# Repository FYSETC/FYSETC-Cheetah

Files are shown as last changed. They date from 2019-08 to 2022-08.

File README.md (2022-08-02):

## 1. Product Introduction

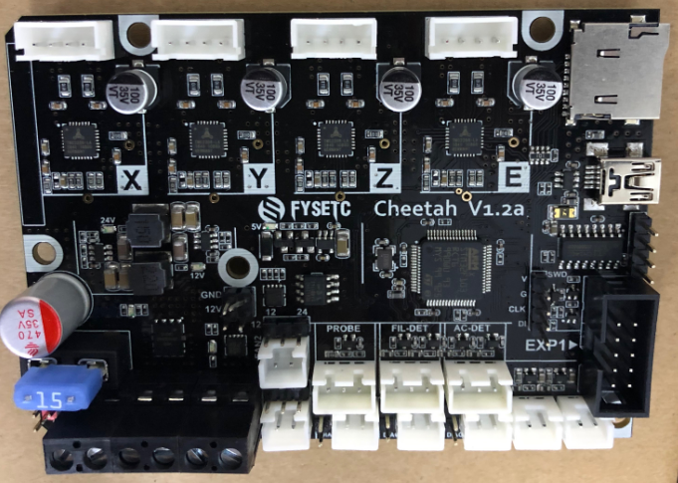
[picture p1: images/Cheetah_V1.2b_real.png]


Designed for a single-head 3D printer, many interfaces are reserved for more features. Such as AC detection, filament detection, leveling with BL-touch or other sensors.

## 2. Features

- Compact size: 101.5mm x 72mm，Compatible with the Creatlity ender 3 motherboard size

- fully integrated all in one solution:
  
  - STM32F103 MCU (Run Marlin 2.0 )
  - CH340 for high speed USB serial connection 
  - (V1.1)4X TMC2209 stepper drivers, Support sensor-less homing
  - (V1.2)4X TMC2208 stepper drivers, not support sensor-less homing

- UNIVERSAL POWER:
  
  - can be used with 7V-35V for motors / heated bed
  - (V1.2)24V to 12V/2A DC-DC for fans
  - integrated high precision power regulators (DC/DC):  5V 1A Max and 3.3V  600mA Max LDO

- Onboard TF card socket

- EXP1 for 12864 display panel (Creality 12864 panel or FYSETC Generic12864)

- Onboard RGB control (V1.2 have no RGB control)

- RGB control and fan control 12V/24V optional (Requires 24V to 12V module)

- PCB：
  
  - High quality, High temperature FR4-TG130 PCB
  - Gold ENIG finishing

## 3. Application

Check `examples` folder for more information.

- 3D printer 
- CNC Device
- Other similar machines

## 4. Hardware

### 4.1 Hardware Reasources

| Board Name | Cheetah |
| --- | --- |
| License | GPL V2.0 |
| Latest Version | V1.0 |
| Extruders | 1 |
| Fixed Fans | 2 Max |
| Controlled Fans | 1 Max |
| Heaters | 1 Max |
| Endstops | 3 Max |
| Temp sens | 2 Max |
| I2C | 1 |
| SWD | 1 |
| Serial port chip | CH340 |
| CPU | STM32F103 |
| CPU Speed ( MHz ) | 72 Mhz |
| Stepper driver | 4X TMC2209 (V1.2 = 2208) |
| Stepper driver  Type | Onboard |
| Input | 12v/24v |
| Output | BED OUT：10A Max ；Heater Out：5A Max |

### 4.2 Connectors and jumpers define(V1.1)

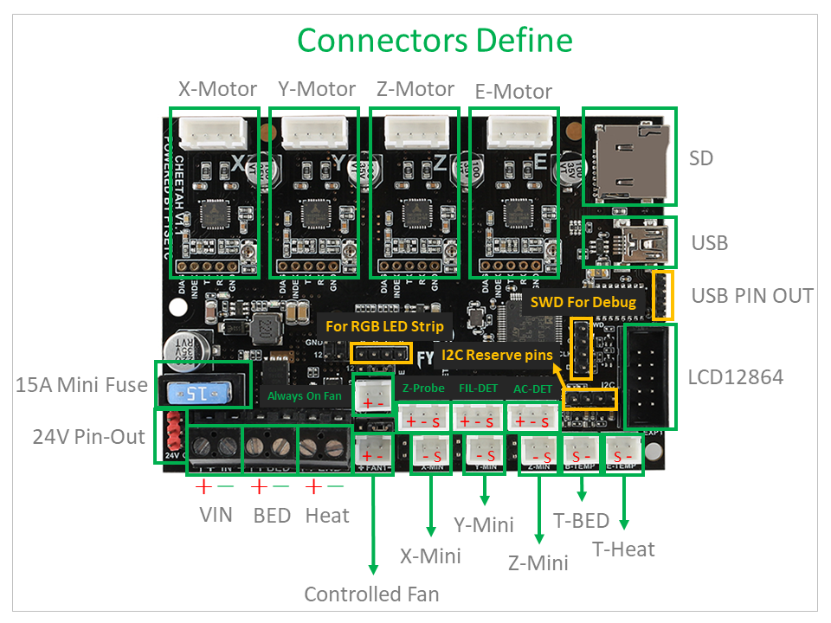
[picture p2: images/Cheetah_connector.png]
Cheetah_connectors

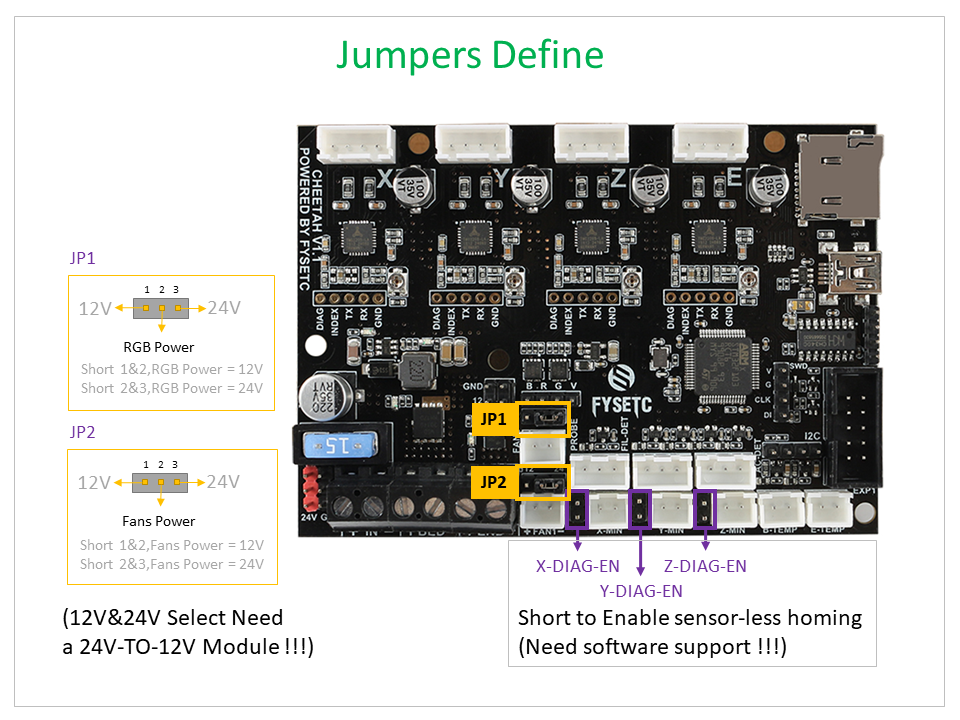
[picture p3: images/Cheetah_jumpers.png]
Cheetah_jumpers


### 4.3 Connectors and jumpers define(V1.2)

Not available.

### 4.4 Pin Definition

#### 4.4.1 Cheetah V1.1

<table>
   <tr><td>Features</td><td>Cheetah Pin</td><td>STM32 Pin</td><td>Pin No.</td><td>Comment</td></tr>
   <tr><td rowspan="3">X-MOTOR(1)</td><td>X-Step</td><td>PB8</td><td>61</td><td></td></tr>
   <tr><td>X-DIR</td><td>PB9</td><td>62</td><td></td></tr>
   <tr><td>X-EN</td><td>PA8</td><td>41</td><td></td></tr>
   <tr><td rowspan="3">Y-MOTOR(2)</td><td>Y-Step</td><td>PB2</td><td>28</td><td></td></tr>
   <tr><td>Y-DIR</td><td>PB3</td><td>55</td><td></td></tr>
   <tr><td>Y-EN</td><td>PB1</td><td>27</td><td></td></tr>
   <tr><td rowspan="3">Z-MOTOR(3)</td><td>Z-Step</td><td>PC0</td><td>8</td><td></td></tr>
   <tr><td>Z-DIR</td><td>PC1</td><td>9</td><td></td></tr>
   <tr><td>Z-EN</td><td>PC2</td><td>10</td><td></td></tr>
   <tr><td rowspan="3">E0-MOTOR(4)</td><td>E0-Step</td><td>PC15</td><td>4</td><td></td></tr>
   <tr><td>E0-DIR</td><td>PC14</td><td>3</td><td></td></tr>
   <tr><td>E0-EN</td><td>PC13</td><td>2</td><td></td></tr>
   <tr><td rowspan="2">TMC2209 SERIAL (UART2)</td><td>TX2</td><td>PA2</td><td>16</td><td></td></tr>
   <tr><td>RX2</td><td>PA3</td><td>17</td><td></td></tr>
   <tr><td rowspan="3">End-stops</td><td>X-MIN</td><td>PA1</td><td>15</td><td></td></tr>
   <tr><td>Y-MIN</td><td>PB4</td><td>56</td><td></td></tr>
   <tr><td>Z-MIN</td><td>PA15</td><td>50</td><td></td></tr>
   <tr><td rowspan="1">FAN</td><td>FAN0</td><td>PC8</td><td>39</td><td></td></tr>
   <tr><td rowspan="3">RGB</td><td>LED-R</td><td>PB0</td><td>26</td><td>Can be used for fan1</td></tr>
   <tr><td>LED-G</td><td>PB7</td><td>59</td><td>Can be used for fan2</td></tr>
   <tr><td>LED-B</td><td>PB6</td><td>58</td><td>Can be used for fan3</td></tr>
   <tr><td rowspan="2">Heating</td><td>E0-Heater</td><td>PC6</td><td>37</td><td></td></tr>
   <tr><td>Heated-Bed</td><td>PC7</td><td>38</td><td></td></tr>
   <tr><td rowspan="2">Temperature</td><td>TE0</td><td>PC4</td><td>15</td><td></td></tr>
   <tr><td>TB</td><td>PC5</td><td>18</td><td></td></tr>
   <tr><td rowspan="8">EXP1</td><td>BEEP</td><td>PC9</td><td>40</td><td></td></tr>
   <tr><td>BTN_ENC</td><td>PC12</td><td>53</td><td></td></tr>
   <tr><td>BTN_EN2</td><td>PC11</td><td>52</td><td></td></tr>
   <tr><td>MISO</td><td>PA6/MISO2</td><td>22</td><td></td></tr>
   <tr><td>BTN_EN1</td><td>PC10</td><td>51</td><td></td></tr>
   <tr><td>SCK</td><td>PA5/SCK2</td><td>21</td><td></td></tr>
   <tr><td>CS</td><td>PA4</td><td>20</td><td></td></tr>
   <tr><td>MOSI</td><td>PA7/MOSI2</td><td>23</td><td></td></tr>
   <tr><td rowspan="2">UART</td><td>TX</td><td>PA9/TX1</td><td>42</td><td></td></tr>
   <tr><td>RX</td><td>PA10/RX1</td><td>43</td><td></td></tr>
   <tr><td rowspan="2">I2C</td><td>I2C2 SCL</td><td>PB10</td><td>29</td><td></td></tr>
   <tr><td>I2C2 SDA</td><td>PB11</td><td>30</td><td></td></tr>
   <tr><td rowspan="3">SWD Debug</td><td>SWDIO</td><td>PA13</td><td>72</td><td>only used for debugging now and can be used for other purposes.</td></tr>
   <tr><td>SWCLK</td><td>PA14</td><td>76</td><td>only used for debugging now and can be used for other purposes.</td></tr>
</table>

#### 4.4.2 Cheetah V1.2

<table>
   <tr><td>Features</td><td>Cheetah Pin</td><td>STM32 Pin</td><td>Pin No.</td><td>Comment</td></tr>
   <tr><td rowspan="3">X-MOTOR(1)</td><td>X-Step</td><td>PB8</td><td>61</td><td></td></tr>
   <tr><td>X-DIR</td><td>PB9</td><td>62</td><td></td></tr>
   <tr><td>X-EN</td><td>PA8</td><td>41</td><td></td></tr>
   <tr><td rowspan="3">Y-MOTOR(2)</td><td>Y-Step</td><td>PB2</td><td>28</td><td></td></tr>
   <tr><td>Y-DIR</td><td>PB3</td><td>55</td><td></td></tr>
   <tr><td>Y-EN</td><td>PB1</td><td>27</td><td></td></tr>
   <tr><td rowspan="3">Z-MOTOR(3)</td><td>Z-Step</td><td>PC0</td><td>8</td><td></td></tr>
   <tr><td>Z-DIR</td><td>PC1</td><td>9</td><td></td></tr>
   <tr><td>Z-EN</td><td>PC2</td><td>10</td><td></td></tr>
   <tr><td rowspan="3">E0-MOTOR(4)</td><td>E0-Step</td><td>PC15</td><td>4</td><td></td></tr>
   <tr><td>E0-DIR</td><td>PC14</td><td>3</td><td></td></tr>
   <tr><td>E0-EN</td><td>PC13</td><td>2</td><td></td></tr>
   <tr><td rowspan="8">TMC2208 SERIAL</td><td>X TX</td><td>PA11</td><td>44</td><td></td></tr>
   <tr><td>X RX</td><td>PA12</td><td>45</td><td></td></tr>
   <tr><td>Y TX</td><td>PB6</td><td>58</td><td></td></tr>
   <tr><td>Y RX</td><td>PB7</td><td>59</td><td></td></tr>
   <tr><td>Z TX</td><td>PB10</td><td>29</td><td></td></tr>
   <tr><td>Z RX</td><td>PB11</td><td>30</td><td></td></tr>
   <tr><td>E TX</td><td>PA2</td><td>16</td><td></td></tr>
   <tr><td>E RX</td><td>PA3</td><td>17</td><td></td></tr>
   <tr><td rowspan="3">End-stops</td><td>X-MIN</td><td>PA1</td><td>15</td><td></td></tr>
   <tr><td>Y-MIN</td><td>PB4</td><td>56</td><td></td></tr>
   <tr><td>Z-MIN</td><td>PA15</td><td>50</td><td></td></tr>
   <tr><td rowspan="2">FAN</td><td>FAN0</td><td>PC8</td><td>39</td><td></td></tr>
   <tr><td>FAN1</td><td>PB0</td><td>26</td><td></td></tr>
   <tr><td rowspan="2">Heating</td><td>E0-Heater</td><td>PC6</td><td>37</td><td></td></tr>
   <tr><td>Heated-Bed</td><td>PC7</td><td>38</td><td></td></tr>
   <tr><td rowspan="2">Temperature</td><td>TE0</td><td>PC4</td><td>15</td><td></td></tr>
   <tr><td>TB</td><td>PC5</td><td>18</td><td></td></tr>
   <tr><td rowspan="8">EXP1</td><td>BEEP</td><td>PC9</td><td>40</td><td></td></tr>
   <tr><td>BTN_ENC</td><td>PC12</td><td>53</td><td></td></tr>
   <tr><td>BTN_EN2</td><td>PC11</td><td>52</td><td></td></tr>
   <tr><td>MISO</td><td>PA6/MISO2</td><td>22</td><td></td></tr>
   <tr><td>BTN_EN1</td><td>PC10</td><td>51</td><td></td></tr>
   <tr><td>SCK</td><td>PA5/SCK2</td><td>21</td><td></td></tr>
   <tr><td>CS</td><td>PA4</td><td>20</td><td></td></tr>
   <tr><td>MOSI</td><td>PA7/MOSI2</td><td>23</td><td></td></tr>
   <tr><td rowspan="2">UART</td><td>TX</td><td>PA9/TX1</td><td>42</td><td></td></tr>
   <tr><td>RX</td><td>PA10/RX1</td><td>43</td><td></td></tr>
   <tr><td rowspan="3">SWD Debug</td><td>SWDIO</td><td>PA13</td><td>72</td><td>only used for debugging now and can be used for other purposes.</td></tr>
   <tr><td>SWCLK</td><td>PA14</td><td>76</td><td>only used for debugging now and can be used for other purposes.</td></tr>
</table>

## 5. Firmware

### 5.1 Marlin

The FYSETC CHEETAH firmware is pre-config for ENDER3 machine, if you want to change the firmware or compile the code yourself , follow the steps.

#### 5.1.1 Download Vscode + platformio

To compile the firmware , you need to install Visual Studio Code and the platformio pulg-in.

#### 5.1.2 Firmware code

You have two code source choices :

##### Source 1

You can get Marlin code is in the `firmware/Marlin` folder in this repository [github](https://github.com/FYSETC/FYSETC-Cheetah/tree/master/firmware/Marlin) or [gitee](https://gitee.com/fysetc/FYSETC-Cheetah/tree/master/firmware/Marlin). 

And change `MOTHERBOARD` define according to your cheetah board version in `Configuration.h`

Cheetah v1.1x

```
#define MOTHERBOARD BOARD_FYSETC_CHEETAH
```

Cheetah v1.2x

```
#define MOTHERBOARD BOARD_FYSETC_CHEETAH_V12
```

##### Source 2

Also you can get upstream branch from [github](https://github.com/MarlinFirmware/Marlin) or [gitee](https://gitee.com/fysetc/Marlin). But remember to change `default_envs` in `platformio.ini` file.

```
default_envs = STM32F103RC_fysetc
```

And change `MOTHERBOARD` define according to your cheetah board version in `Configuration.h`

Cheetah v1.1x

```
#define MOTHERBOARD BOARD_FYSETC_CHEETAH
```

Cheetah v1.2x

```
#define MOTHERBOARD BOARD_FYSETC_CHEETAH_V12
```

You'd better change your configuration base on the configuration on github [cheetah v1.1](https://github.com/MarlinFirmware/Configurations/tree/import-2.0.x/config/examples/Creality/Ender-3/FYSETC%20Cheetah)/[cheetah v1.2](https://github.com/MarlinFirmware/Configurations/tree/import-2.0.x/config/examples/Creality/Ender-3/FYSETC%20Cheetah%201.2) or gitee [cheetah v1.1](https://gitee.com/fysetc/Configurations/tree/import-2.0.x/config/examples/Creality/Ender-3/FYSETC%20Cheetah)/[cheetah v1.2](https://gitee.com/fysetc/Configurations/tree/import-2.0.x/config/examples/Creality/Ender-3/FYSETC%20Cheetah%201.2).

#### 5.1.3 Compile the firmware

Open Vscode and open platformio main page and click the "Open Project" button , and direct to the folder where you put your firmware.

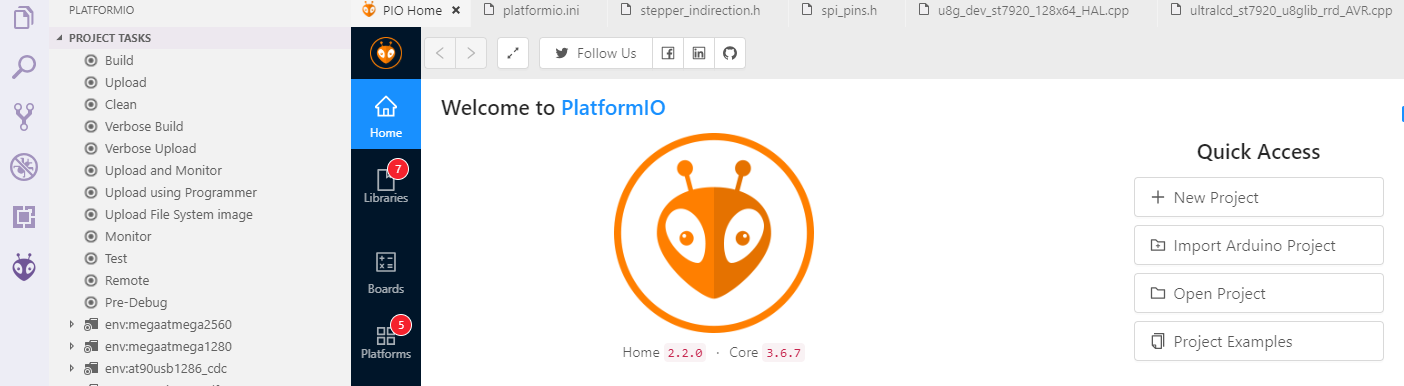
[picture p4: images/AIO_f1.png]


If everything goes fine , at the bottom you can see several buttons



Just click check mark to compile.

Note: If you generate the hex file fail you may need to open vscode using Administrator Account .

### 5.2 Klipper

#### 5.2.1 Requirement

Our Cheetah board have CH341 chip, so you may need to install its driver. There are a lot of CH341 driver if you search on the internet, links below may help.

[Ch34x](https://github.com/gorgiaxx/CH34x-Driver-Linux)

#### 5.2.2 Compile firmware

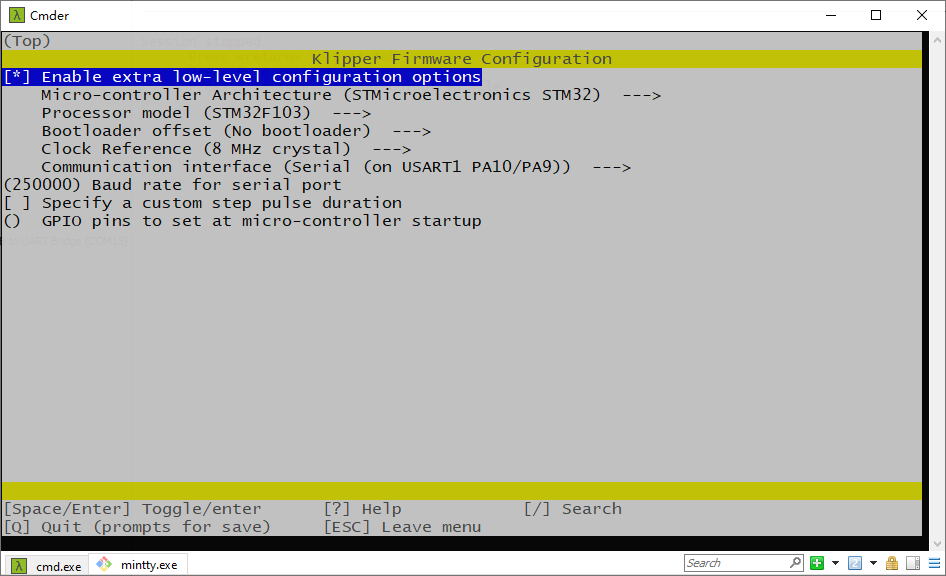
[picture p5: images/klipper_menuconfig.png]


If you want to use sdcard bootloader, you can follow the instructions [github](https://github.com/FYSETC/FYSETC-Cheetah/tree/master/bootloader) or [gitee](https://gitee.com/fysetc/FYSETC-Cheetah/tree/master/bootloader).

After you upload the firmware, please power down Cheetah first, then power on again.  And use the following octoprint parameter.

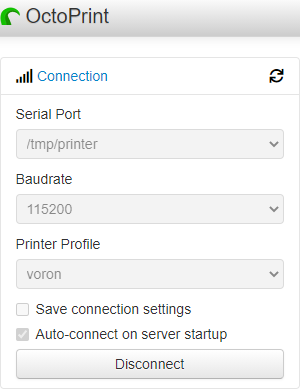
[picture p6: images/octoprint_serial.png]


### 5.2.3 printer.cfg

You can change your config according to you machine base on the generic printer.cfg from Klipper [here(Cheetah_v1.1)](https://github.com/Klipper3d/klipper/blob/master/config/generic-fysetc-cheetah-v1.1.cfg) and [here(Cheetah_v.12)](https://github.com/Klipper3d/klipper/blob/master/config/generic-fysetc-cheetah-v1.2.cfg). Or our example config in `Firmware\Klipper\Cheetah**` folder [here](https://github.com/FYSETC/FYSETC-Cheetah/tree/master/firmware/Klipper/Cheetah-v1.2). 

### 5.3 Upload the firmware

We provide several methods for you to upload the firmware . But first, you need to install CH340x driver, please check here: [CH340 driver](https://www.wch.cn/search?t=all&q=CH340).

#### Method 1:  Upload the firmware with sdcard

You need to upload `bootloader` first, please follow the `README` in `bootloader` folder in this repository. Well, link is [github](https://github.com/FYSETC/FYSETC-Cheetah/tree/master/bootloader) or [gitee](https://gitee.com/fysetc/FYSETC-Cheetah/tree/master/bootloader).

#### Method 2: Upload the firmware(windows,linux,Mac) - for Marlin

This method only works for Marlin. You can just click the upload button in platformio to upload the firmware.



#### Method 3: Upload the firmware(windows)

This method only works in windows system. 

After compiling , you should see the firmware file `firmware.hex` in the folder `FIRMWARE_LOCATE\Marlin\Marlin\.pio\build\STM32F103RC_fysetc\`

You can follow the following steps to upload the firmware.

- Download the flash software in our [github](https://github.com/FYSETC/STM32Flasher) or [gitee](https://gitee.com/fysetc/STM32Flasher).

- Power the board with power supply and connect the board to your PC with USB cable

- Double the click "FlyMcu.exe" software

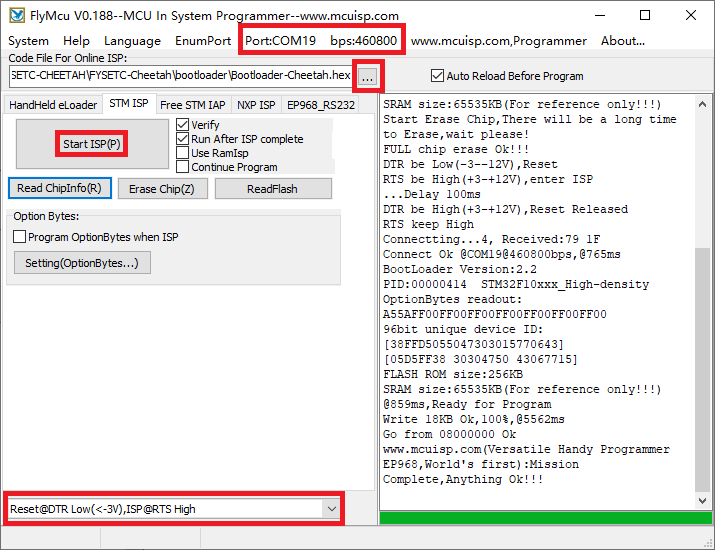
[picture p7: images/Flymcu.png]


- Select `Reset@DTR low(<-3v),ISP @RTS High`

- Click "Port" to select the port of your USB 

- Select `firmware.hex` in the `Code File For Online ISP:` edit box. This the firmware you built. There is pre-build firmware file named `klipper.hex` on [github](https://github.com/FYSETC/FYSETC-Cheetah/tree/master/firmware/Klipper/Cheetah-v1.2) or [gitee](https://gitee.com/fysetc/FYSETC-Cheetah/tree/master/firmware/Klipper/Cheetah-v1.2). If you use marlin, pre-build firmware is on [github](https://github.com/FYSETC/FYSETC-Cheetah/tree/master/examples/Ender-3) or [gitee](https://gitee.com/fysetc/FYSETC-Cheetah/tree/master/examples/Ender-3).

- At last, click  `Start ISP(p)` button to upload the firmware.

#### Method 4: Upload the firmware(Klipper)

This method is only for Klipper firmware. According to the method from Klipper config file for Cheetah [here](https://github.com/KevinOConnor/klipper/blob/master/config/generic-fysetc-cheetah-v1.1.cfg) and [here](https://github.com/KevinOConnor/klipper/blob/master/config/generic-fysetc-cheetah-v1.2.cfg). You can run the command

```
stm32flash -w out/klipper.bin -v -i rts,-dtr,dtr /dev/ttyUSB0
```

#### Method 5: Upload the firmware(linux)

This method only works in Linux system.

- ##### Load usb driver

Delete the old version driver /lib/modules/$(uname -r)/kernel/drivers/usb/serial/ch341.ko

```
rm /lib/modules/$(uname -r)/kernel/drivers/usb/serial/ch341.ko
```

Download the CH34x driver(linux version) from our [github](https://github.com/FYSETC/CH340-Driver) or [gitee](https://gitee.com/fysetc/CH340-Driver).

Follow the `readme.txt` to make and load the driver.

If you want the driver load automatically every time your PC power up. You can copy the ch34x.ko file to 

directory /lib/modules/$(uname -r)/kernel/drivers/usb/serial/ , and do

```
depmod 
```

- ##### Install stm32flash tool

First get the code

```
git clone https://git.code.sf.net/p/stm32flash/code stm32flash-code
```

Then follow the INSTALL file to install the software

- ##### Upload the firmware

Connect the motherboard with USB cable and your PC. And do

```
dmesg
```

And you will get message like 



the ttyUSB0 is the port to communicate with the motherboard.

And then go the `firmware.hex` file location directory and do the follow command to upload the firmware

```
 stm32flash -w firmware.hex -v -i rts,-dtr /dev/ttyUSB0
```

## 6. Version

----------------

V1.1：

1. Initial version

V1.2a：

1. Change 2209 to 2208 and support 2208 UART mode
2. Add a controlled fan for hotend
3. And a 24 to 12V/2A Circuit for fans and mosfets
4. Add mosfet driver chip
5. Remove the RGB circuit and I2C pins
6. Change the 4P pin header（1.1 is USB pinout） to UART1
7. Fixed USB voltage reflow to PSU issue

V1.2b：

1. Fix some silks mark
2. Update MOSFET drive circuit

## 7. FAQ：

--------------------

### 1. Why use USB-TO-UART chip for USB？

We just want to give you a convenient way to update the firmware without having to think about which bootloader to use and how to jumper BOOT0&BOOT1.
Also, if your board is already installed in the machine, the jumper setting is more inconvenient for you.
So, by adding a chip that can solve the problem, why not do it?

### 2. Why does the USB power flow back to the PSU?

At the time of design, we thought that plugging in the USB is just to update the firmware, and at other times you will use the SD card for printing. Even if you use USB printing, it should be a short-time debugging.
Even, we found that most of the 2560 boards did the same, and nothing went wrong. This should be a way of testing over time.
Until TH3D promotes this problem in the whole world, I think this will cause confusion for many people, so I will solve this problem whether or not it will cause problems, and it was already solved on the 1.2a version.

### 3. The direction of the encoder is wrong？

First of all, this is not a hardware problem, we can adjust it through software, and it is very easy.
Secondly, there is no fixed standard in this direction, and different people may not like the same.
Finally, we have changed to the most favorite way, if you want to reverse, you can also set the firmware yourself.
***Note: In fact, our price is only the price of a hardware platform, we have never calculated the value of software, we think that as one of the contributors and users of marlin, we should follow the spirit of open source, make more people easier Get the convenience of open source. Instead of selling it with open source resources.***

### 4. The screen displays garbled characters？

First of all, we should know that low-voltage signals are easily interfered, so we should try to avoid the screen line and the high-voltage and high-current lines being too close.
In addition, our people usually have static electricity on their hands, and directly touch some electronic components, which may also affect normal signal transmission.
So if it is just an accidental phenomenon and it will disappear after re-power, then don't worry.
If it has been there, please contact us and we will deal with it according to the specific situation!

### 5. Y-motor got very hot

Actually there is an inappropriate firmware configuration.
You need to change

```
 #define CHOPPER_TIMING CHOPPER_DEFAULT_12V
```

to 

```
 #define CHOPPER_TIMING CHOPPER_DEFAULT_24V
```

### 6. Can't save config to eeprom

This is a firmware issue that has been fixed so far, you can fix it by upgrading the firmware.
For new firmware,the default config is not for cheetah board anymore as we have other boards to release and the need to build the firmware, you need to change default_envs to fysetc_STM32F1 in platformio.ini file and replace the configuration.h and configuration_adv.h file with FYSETC example config. 

**We will continue to update, please look forward to it!***

## 8. Tech Support

---

Please submit any technical issue into our [forum](http://forum.fysetc.com/)

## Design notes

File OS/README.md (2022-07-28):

# OS

## SAMFi-OS_OrangePi_zero

Before you config the [SAMF-OS_OrangePi_zero](https://github.com/FYSETC/FYSETC-SAMFi-OS). You need an TF card with at least 8G capacity.

### Step 1

Download and flash the OS image with `balenaEtcher` software to your TF card. Insert your flashed TF card to OrangePi-zero and connect Ethernet cable then power on. Find the ip address of OrangePi-zero on your router, host name is `orangepizero`.

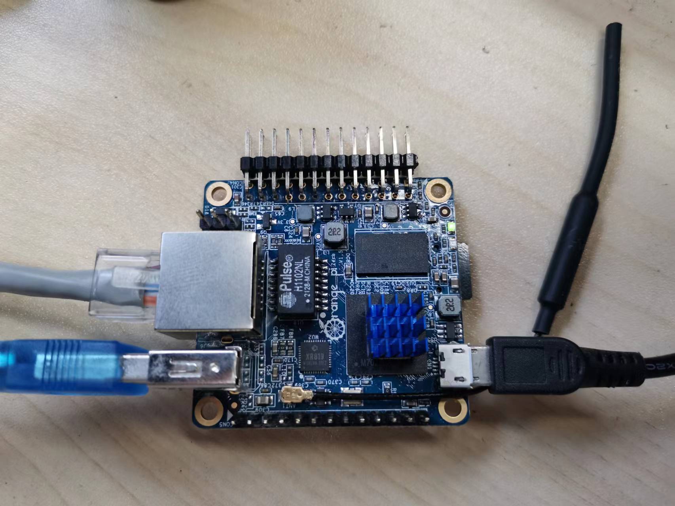
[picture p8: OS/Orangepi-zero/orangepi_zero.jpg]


### Step 2

You can find the firmware `klipper.bin` in `Orangepi-zero` folder after you download the github repository. It is also stay in the OS path `firmwares\cheetah1.2.bin` after you login the OS with SSH.

Original SSH account and password:

```
account: fysetc
password: fysetc123
```

Flash the firmware with the command below after you connect your OrangePi and Cheetah with USB cable.

```
stm32flash -w firmwares/cheetah1.2.bin -v -i rts,-dtr,dtr /dev/ttyUSB0
```

Or follow the instructions [here](https://github.com/FYSETC/FYSETC-Cheetah#53-upload-the-firmware) for firmware uploading.

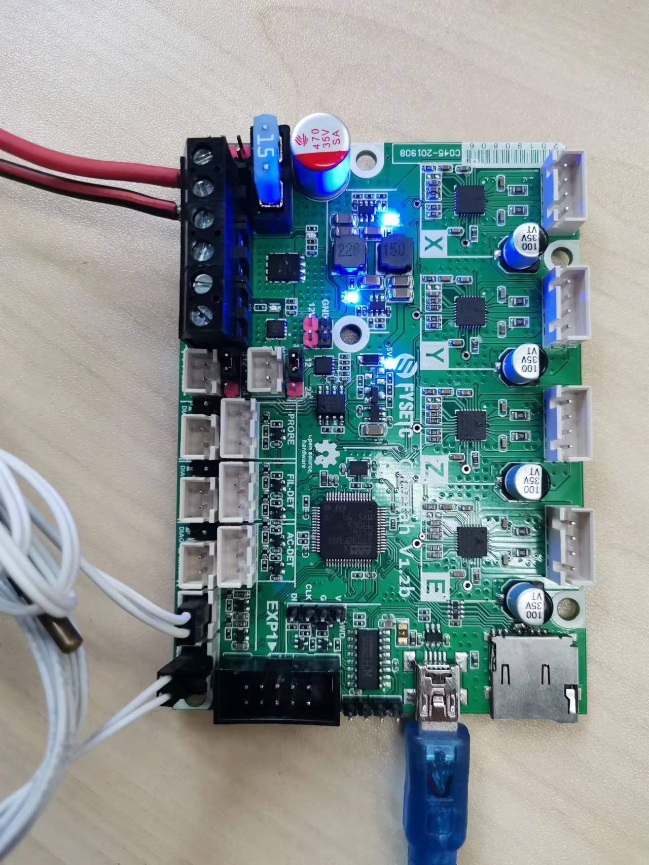
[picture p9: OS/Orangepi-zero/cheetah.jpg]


### Step 3:

Prepare the `pinter.cfg`, using the command below

```
cp klipper_config/cheetah1.2.cfg firmware/printer.cfg
```

You probably need to change `id` by `ls /dev/serial/by-id` command.

I use the generic klipper config for this example, you need to change the config according to your machine. Now visit the webpage with your orangepi-zero IP address. Good to go.

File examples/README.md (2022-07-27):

# Examples

This folder will contains machines that Cheetah board support. If you can't find your printer here , it does not mean Cheetah board does not support it , just because we don't add it at the moment. We strongly encourage you to make PR  for us and here is the [tutorial](https://docs.github.com/en/free-pro-team@latest/github/collaborating-with-issues-and-pull-requests/creating-a-pull-request). Thanks for your support.

## OrangePi-zero

We build an image base on `Armbian_20.11.6_Orangepizero_buster_current_5.10.4` mainsail OS for OrangePi-zero. You can download it from [Dropbox](https://www.dropbox.com/s/6tvu6on8kcejoij/Armbian_20.11.6_Orangepizero_buster_current_5.10.4_Cheetah_mainsail.img.ima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) and [百度云盘](https://pan.baidu.com/s/1XPlh9ovenJcJELMntx0g-w)（
提取码：1357）, remember you need an TF card with at least 8G capacity. The information of this image below.

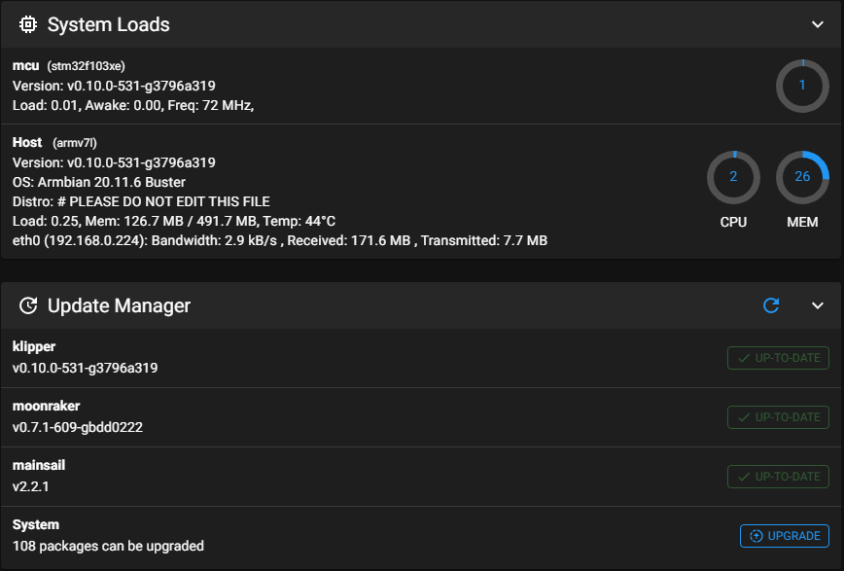
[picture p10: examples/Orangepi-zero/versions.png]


### Step 1

Download and flash the OS image with `balenaEtcher` software to your TF card. Insert your flashed TF card to OrangePi-zero, and power on it. Connect Ethernet cable to OrangePi-zero. And find the ip address of OrangePi-zero from your router.



### Step 2

You can find the firmware `klipper.bin` in `Orangepi-zero` folder after you download the github repository. It is also stay in the OS path `klipper\out\klipper.bin` after you login the OS with SSH.

Original SSH account and password:

```
account: fysetc
password: fysetc123
```

Flash the firmware with the command below after you connect your OrangePi and Cheetah with USB cable.

```
stm32flash -w out/klipper.bin -v -i rts,-dtr,dtr /dev/ttyUSB0
```

Or follow the instructions [here](https://github.com/FYSETC/FYSETC-Cheetah#53-upload-the-firmware) for firmware uploading.



### Step 3:

I use the generic klipper config for this example, you need to change it according to your machine. Now visit the webpage with your orangepi-zero IP address. Good to go.

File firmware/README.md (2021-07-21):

## Firmware

### Marlin

Marlin firmware is base on the upstream [Marlin 2.0.x](https://github.com/MarlinFirmware/Marlin/tree/2.0.x). And it is preconfig for Creality Ender-3 machine using FYSETC CHEETAH V1.2 motherboard.

And there are pre-build firmwares for some example machines, you can find it on [github](https://github.com/FYSETC/FYSETC-Cheetah/tree/master/examples) or [gitee](https://gitee.com/fysetc/FYSETC-Cheetah/tree/master/examples).

### Klipper

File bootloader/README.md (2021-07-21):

# Bootloader
This is the bootloader for FYSETC Cheetah board.

## Upload bootloader

### Method 1: Upload the bootloader(windows)

This method only works in windows system. You can follow the following steps to upload the bootloader.

- Download the flash software in our github https://github.com/FYSETC/STM32Flasher

- Power the board with power supply and connect the board to your PC with USB cable

- Double the click `FlyMcu.exe` software

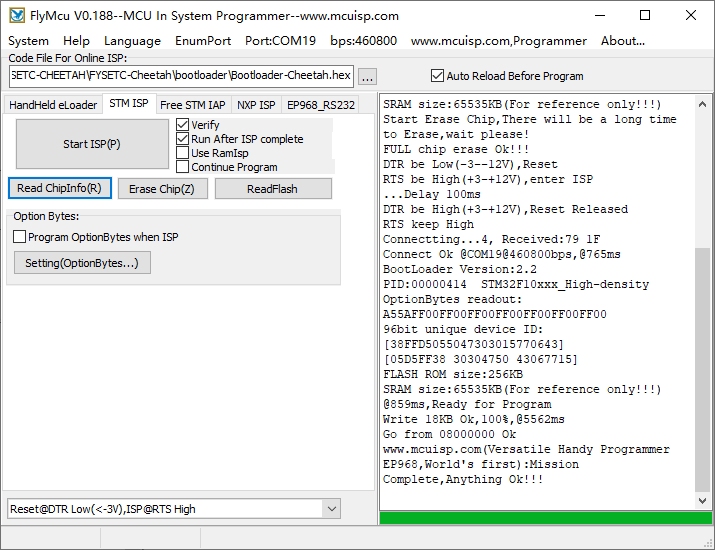
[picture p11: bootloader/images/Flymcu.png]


- Select `Reset@DTR low(<-3v),ISP @RTS High`

- Click "Port" to select the port of your USB 

- Select `Bootloader-Cheetah.hex` in the `Code File For Online ISP:` edit box. There is bootloader file named `Bootloader-Cheetah.hex` beside this `README` file. 

- At last, click  `Start ISP(p)` button to upload the firmware.

### Method 2 : Upload the bootloader(linux)

This method only works in Linux system.

#### Load usb driver

Delete the old version driver `/lib/modules/$(uname -r)/kernel/drivers/usb/serial/ch341.ko`

```
rm /lib/modules/$(uname -r)/kernel/drivers/usb/serial/ch341.ko
```

Download the CH34x driver(linux version) from our github

https://github.com/FYSETC/CH340-Driver

follow the `readme.txt` to make and load the driver .

If you want the driver load automatically every time your PC power up. You can copy the `ch34x.ko` file to 

directory `/lib/modules/$(uname -r)/kernel/drivers/usb/serial/` , and do

```
depmod 
```

#### Install stm32flash tool

First get the code

```
git clone https://git.code.sf.net/p/stm32flash/code stm32flash-code
```

Then follow the INSTALL file to install the software

#### Upload the bootloader

Connect the motherboard with USB cable and your PC. And do

```
dmesg
```

And you will get message like 



the ttyUSB0 is the port to communicate with the motherboard.

And then go the `Bootloader-Cheetah.hex` file location directory and do the follow command to upload the firmware

```
 stm32flash -w Bootloader-Cheetah.hex -v -i rts,-dtr /dev/ttyUSB0
```

## Follow-up work

### Marlin firmware

This bootloader default boot address is `0x8005000`, so if you want to use this bootloader you need to change the firmware  flash address to `0x8005000`.

You need to add the following lines to Marlin file `Marlin\buildroot\share\PlatformIO\scripts\fysetc_STM32F1.py`

```
# Relocate firmware from 0x08000000 to 0x08005000
for define in env['CPPDEFINES']:
    if define[0] == "VECT_TAB_ADDR":
        env['CPPDEFINES'].remove(define)
env['CPPDEFINES'].append(("VECT_TAB_ADDR", "0x08005000"))

custom_ld_script = os.path.abspath("buildroot/share/PlatformIO/ldscripts/fysetc_stm32f103rc.ld")
for i, flag in enumerate(env["LINKFLAGS"]):
    if "-Wl,-T" in flag:
        env["LINKFLAGS"][i] = "-Wl,-T" + custom_ld_script
    elif flag == "-T":
        env["LINKFLAGS"][i + 1] = custom_ld_script
```

You can add it after the line 

```
Import("env")
```

And change the following line in `Marlin\buildroot\share\PlatformIO\ldscripts\fysetc_stm32f103rc.ld`

```
rom (rx)  : ORIGIN = 0x08005000, LENGTH = 256K - 20K
```

And then rebuild the firmware.

### Klipper firmware

You need to select `20KiB bootloader`

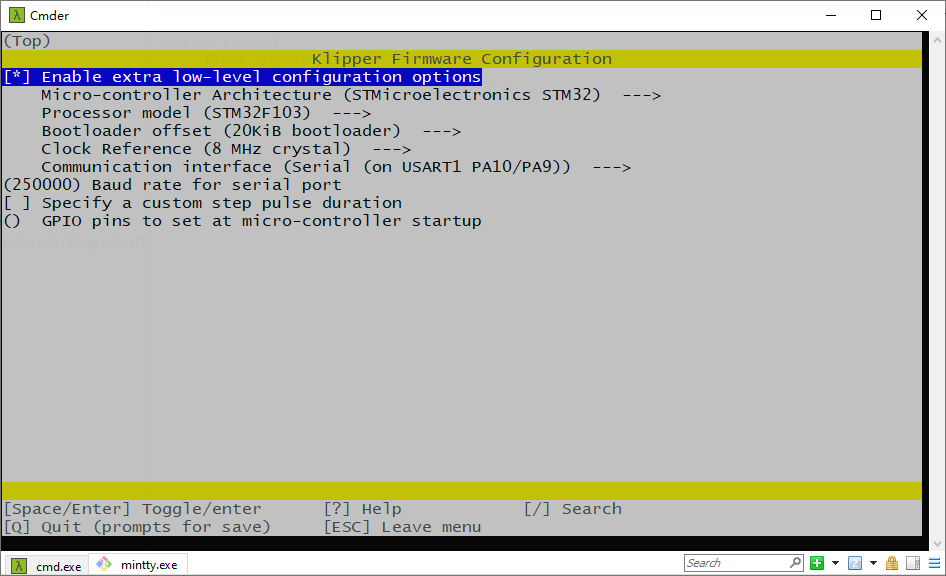
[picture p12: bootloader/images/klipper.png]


**After you upload the firmware, please power down Cheetah first, then power on again.  And use the following octoprint parameter.**



## Upload firmware with sdcard

After you upload the bootloader and build the firmware, now you can upload it to the board with sdcard

1. Copy the `firmware.bin`( if you use `Klipper` firmware, please rename `klipper.bin` to `firmware.bin`) file to the SD card , you need to be sure the firmware name is `firmware.bin`. 
2. And then power off the machine.
3. Insert the SD card to the board.
4. Power on the machine. 
5. And wait for 20~40 seconds (larger the firmware, more time need), it will be done. 

You can check if the `firmware.bin` file in the sdcard have been changed to `old.bin`, if so, means success. if not: Try to upload the `bootloader` again or open an issue in our [github](https://github.com/FYSETC/FYSETC-Cheetah/issues).

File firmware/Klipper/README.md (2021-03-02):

# Klipper

This is the example pre-build firmware of Klipper for Cheetah boards ,you can follow the Cheetah firmware [upload instruction](https://github.com/FYSETC/FYSETC-Cheetah#upload-the-firmwarewindowslinuxmac) to upload it to Cheetah board.

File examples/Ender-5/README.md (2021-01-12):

# Ender5

This setup up guide is for installing FYSETC Cheetah to Ender5 machine.

## Firmware

Replace Marlin with `configuration.h` and `configuration_adv.h` beside this README file. Then compile and upload.

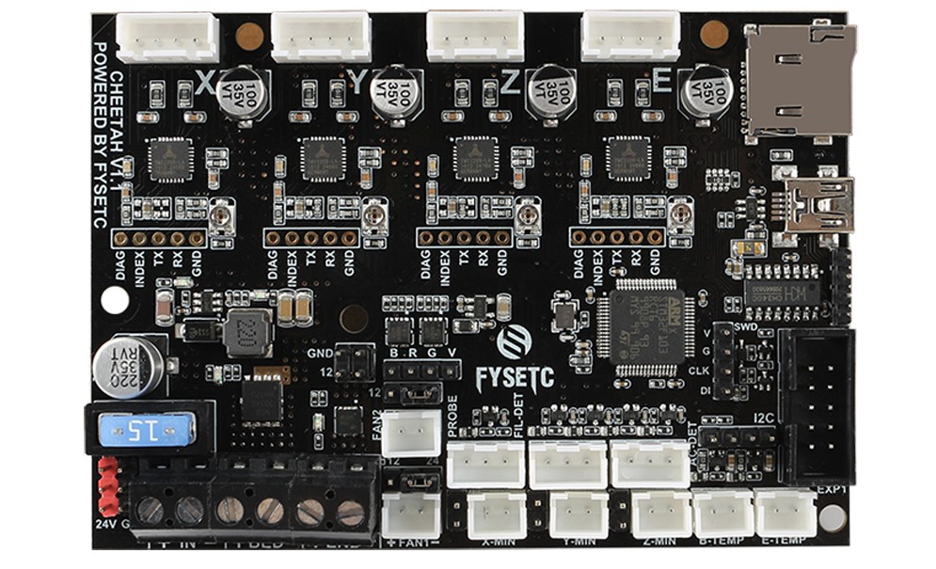
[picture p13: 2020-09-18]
images/Cheetah_Real.jpg

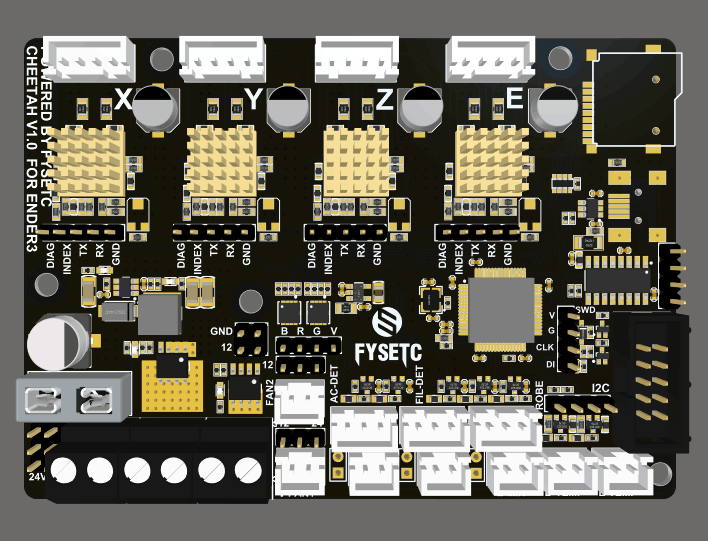
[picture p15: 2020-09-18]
images/Cheetah_top.png

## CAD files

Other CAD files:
hardware/1.1/Cheetah_MainBoard_V11.DWG

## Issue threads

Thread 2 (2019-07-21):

Unable to upload the firmware to the Cheetah v1.1 board

EnnajimiYassine, 2019-07-21:
I'm unable to upload the firmware to my cheetah v1.1 , I tried to upload with a mac and a raspberry pi but I get the same error. Am I missing something ? :
stm32flash 0.5
http://stm32flash.sourceforge.net/
Using Parser : Intel HEX
Interface serial_posix: 57600 8E1
GPIO sequence start
setting port signal rts to 1... OK
delay 100000 us
setting port signal dtr to 0... OK
GPIO sequence end
Failed to init device

Thank you for your help

puccac, 2019-10-11:
Programs required for firmware upload in Windows

Git CMD
https://git-scm.com/downloads
Download for Windows

stm32flash
https://sourceforge.net/projects/stm32flash/
Download stm32flash-0.5-win64.zip

How to upload firmware

3d Turn off the printer, connect the computer to the board with a USB cable, and check the COM port.

open git cmd
cd Downloads \ stm32flash-0.5-win64 <-stm32flash path

Read information
stm32flash -b460800 COM3 <-change after checking the port

Write firmware
stm32flash -R -b460800 -w firmware.hex -v -i rts, -dtr, dtr COM3 <-change after checking the port

empakoso, 2019-10-16:
OctoPrint will also work.  I just used plug-in Firmware Updater and STM32 drivers (see the Firmware Updater GitHub page to perform STM32 drivers using RPi SSH).  Settings:
Flash method (select) "stm32flash (STM32 built-in bc..."
Set the path to stm32flash (type) "/usr/bin/stm32flash"
Test (click result) "The path is valid"

I was able to connect and flash successful using the hex file

db414813, 2019-12-01:
I have same issue as OP. I have the required software but get same error as OP. Any resolution to this? I really don't want to have to flash an rpi with octoprint when I should not have to.

db414813, 2019-12-02:
I gave up and followed the rpi octopi route. Flash was successful per octopi. I will report back any issues. I am still not sure why my linux desktop could not flash the firmware to the cheetah board.

Magoo0876, 2020-01-30:
Connect the board to the octopi.
Open a linux command line with:
    ssh pi@octopi.local
enter the password: raspberry
or if changed what you have chosen
check your usb connection
   dmesg |grep usb

there should  be something like that:
[ 1078.737260] usb 1-1.4: new full-speed USB device number 6 using dwc_otg
[ 1078.870413] usb 1-1.4: New USB device found, idVendor=1a86, idProduct=7523, bcdDevice= 2.63
[ 1078.870428] usb 1-1.4: New USB device strings: Mfr=0, Product=2, SerialNumber=0
[ 1078.870438] usb 1-1.4: Product: USB2.0-Serial
[ 1078.874440] **usb 1-1.4: ch341-uart converter now attached to ttyUSB0**

You should see a correct connection. Procced with flashing.
If not update the raspberry pi.
type:
    sudo apt full-upgrade

   sudo reboot
#type:
    ls /dev/serial/by-id/

Enter the id in the next command

    stm32flash -w /home/pi/yourfirmwarefile.bin -v -i rts,-dtr,dtr /dev/serial/by-id/enteryouridhere

hth regards Magoo

Jugulaire, 2020-06-02:
No, it's not working on any of my machine. Tested on OPI one,Zero Raspberrypi 2,3,4 and finally with my Lenovo T450 and X220? no luck ...

```bash
┌🤘-🐧jugu@ 💻 W0RKST4TI0N - 🧱 11F5-30EA
└🤘-> sudo stm32flash -w firmware.bin -v -i rts,-dtr,dtr /dev/ttyUSB0 -R
[sudo] Mot de passe de jugu :
stm32flash 0.5

http://stm32flash.sourceforge.net/

Using Parser : Raw BINARY
Interface serial_posix: 57600 8E1

GPIO sequence start
 setting port signal rts to 1... OK
 delay 100000 us
 setting port signal dtr to 0... OK
 delay 100000 us
 setting port signal dtr to 1... OK
GPIO sequence end

Failed to init device.
```

sixtyfive, 2021-08-05:
Same problem. Output of `stm32flash /dev/ttyUSB0`:

```
stm32flash 0.6

http://stm32flash.sourceforge.net/

Interface serial_posix: 57600 8E1
Version      : 0x22
Option 1     : 0x00
Option 2     : 0x00
Device ID    : 0x0414 (STM32F10xxx High-density)
- RAM        : Up to 64KiB  (512b reserved by bootloader)
- Flash      : Up to 512KiB (size first sector: 2x2048)
- Option RAM : 16b
- System RAM : 2KiB
```

output of `stm32flash -w out/klipper.bin -v -i rts,-dtr,dtr /dev/ttyUSB0`:

```
stm32flash 0.6

http://stm32flash.sourceforge.net/

Using Parser : Raw BINARY
Interface serial_posix: 57600 8E1

GPIO sequence start
 setting port signal rts to 1... OK
 delay 100000 us
 setting port signal dtr to 0... OK
 delay 100000 us
 setting port signal dtr to 1... OK
GPIO sequence end

Failed to init device.
```

Please help!

Magoo0876, 2021-08-05:
try:

**dmesg |grep tty**

and look if ttyUSB0 is the correct device.

pi@mainsailos:~/klipper $ dmesg |grep tty
[    0.000000] Kernel command line: coherent_pool=1M 8250.nr_uarts=0 snd_bcm2835.enable_compat_alsa=0 snd_bcm2835.enable_hdmi=1 bcm2708_fb.fbwidth=720 bcm2708_fb.fbheight=720 bcm2708_fb.fbswap=1 vc_mem.mem_base=0x3ec00000 vc_mem.mem_size=0x40000000  console=ttyS0,115200 console=tty1 root=PARTUUID=1b18721f-02 rootfstype=ext4 elevator=deadline fsck.repair=yes rootwait
[    0.001187] printk: console [tty1] enabled
[    3.290891] 3f201000.serial: ttyAMA0 at MMIO 0x3f201000 (irq = 114, base_baud = 0) is a PL011 rev2
[964733.566065] usb 1-1.5: **ch341-uart converter now attached to ttyUSB0**

If this is ok the set the flash command two times immediately one after one.
At my board it always works at the second attempt.

Try another usb cable even if the device is correctly connected and visible at the linux os.

Magoo0876, 2021-08-05:
This is my actual right now tested command for flashing.
Check the /dev/serial/by-id folder if there is a file called like the last part of the command below. If not change it to your USB id.

stm32flash -w /home/pi/klipper/out/klipper.bin -v -i rts,-dtr,dtr /dev/serial/by-id/**usb-1a86_USB2.0-Serial-if00-port0**

sixtyfive, 2021-08-05:
Hi @Magoo0876, thanks for the quick response!

I'd tried with both `/dev/serial/by-id/usb-1a86_USB2.0-Serial-if00-port0`, as well as `/dev/ttyUSB0` (making sure it's the only / correct one) before; no difference. I had also been playing with the GPIO sequence, as various places (Wiki, Issues, forums) give different recommendations (so far have seen: `rts,-dtr,dtr`, `rts,-dtr`, `rts,dtr`). I've also tried: multiple times one after the other manually; multiple times in a `for` loop; a script polling for `/dev/serial/by-id/usb-1a86_USB2.0-Serial-if00-port0` and then sending the command right after the board is plugged in. All to no avail.

What I've not tried is a different cable ... I'll go out and try to find another one today!

sixtyfive, 2021-08-05:
Okay, so I went out today and searched shops until I found a mini USB cable. It cost 11€ for 75cm and is "premium shielded" (whatever that's supposed to mean, only some marketing person will know). Unfortunately it doesn't change a thing. Still `Failed to init device.` Now having two cables, I cut the +5V on one of them to get rid of the backfeed problem while powered from +12V. Again, no change (wouldn't have expexted one). Always trying at least twice in a row by the way.

Unless you have any more ideas, I'll go out and get an stlinkv2 and try via the SWD header :-/

Magoo0876, 2021-08-05:
So that's not nice. What you can still try is to update your os.

If you are on an raspberry or Debian base type:

**sudo apt update && apt full-upgrade**
and for the firmware of the pi

**sudo rpi-update**

In the past there was a problem with the ch340/341 driver which I also ran into it.
If this still does not do the job, flash the stock firmware via sd card to the cheetah board to look if the board is ok.
Then copy the Klipper.bin file to the sd and try it this way.
I also attached my firmware. To use it you have to rename it!

[klipper.txt](https://github.com/FYSETC/FYSETC-Cheetah/files/6940966/klipper.txt)

Good luck.

sixtyfive, 2021-08-05:
Okay, so, it just worked. I didn't try another time; bit scared to break something. The command that eventually made it work was:

```
stm32flash -w out/klipper.bin -v -i rts /dev/serial/by-id/usb-1a86_USB2.0-Serial-if00-port0
```

For the record, my board is version 1.1b and my laptop is running Manjaro Linux (I tend to keep all packages up-to-date quite pedantically). Kernel version at the time of this writing was 5.10.53.

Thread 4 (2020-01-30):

Cheetah 1.1b Display problem if usb connected

Magoo0876, 2020-01-30:
My board has a problem with the usb connector. It is no problem to flash or update the board, but if you connect the power supply and the usb the 5V for the display drop to 4,4V. Is the board defektive or is that a general ? There are no schematics for that board, I bought it because of open source. So please provide the missing documentation.

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

Magoo0876, 2020-12-19:
This problem can be mitigated by desoldering the fuse close by the usb port und adding a removable jumper instead.

Closed 2020-12-19.

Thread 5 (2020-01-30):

Cheetah 1.1b is not supported by Klipper Firmware!!!!!

Magoo0876, 2020-01-30:
Due to a different board design compared to 1.1 and 1.2 the Klipper bootloader does not work for that at the moment. Maybe it can solve in the future when the documentation is available.

Magoo0876, 2020-12-19:
The problem is already been solved and the board is woking very good with Klipper.

Closed 2020-12-19.

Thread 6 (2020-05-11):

Cheetah 1.2 Usb cable cause dimmed LCD

Shaka-60hp, 2020-05-11:
Hi, I'm happy with the board, but I have this problem that bothers me
When I connect the USB cable to any (and I mean ANY) computer , the lcd dims almost unreadable
Main cause seems to be that the USB from the computer messes up by sending voltage to the board

So I took the liberty of creating a modded USB cable, with no power, only data, and it works fine.

The question remains, why this is happening? how you can fix it and how I get a soluttion to this problem.

Thanks
Pablo

RudolphRiedel, 2020-05-24:
This is an issue with the new circuit to switch between USB power and 5V from the PSU.
The circuit is not really working.
First thing is Q1 has drain and source switched but this is not the issue.
When you use both the PSU and USB, both Q1 and Q2 are switched off.
The PSU will still power the board though as the current runs thru the body-diode of Q2, this is causing a drop in the 5V though and therefore the LCD will dimm down.

A patch for this issue, not a fix, would be to remove D5 and R63 from the board.
And as it has been reported on Facebook that not drawing current from the USB might result in disconnecting the USB itself, I suggested to solder a 1k resistor across C37 as a base load.

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

sl1pkn07, 2022-09-16:
Hi

i'ts me, or the board 1.1 have the same issue when power the board througth usb? (only USB). i get 3.8v in +5v->GND EXP1 pins. the ender 3 display is almost zero readable

greetings

RudolphRiedel, 2022-09-17:
The 1.1 board is completely different in this regard as it uses the diode D14 to connect USB_5V to 5V and does not switch off the 5V from the regulator.
But since small rectifier diodes can have a voltage drop of over 1V and 5V from USB mostly is only what we can hope for, a resulting voltage of 3.8V is plausible.
So, not the same issue but the same result.

Since the printer can not be used with USB only anyways, just juse the port for programming only.

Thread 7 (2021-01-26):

Default FYSETEC Cheetah bootloader

alhim, 2021-01-26:
Where I can found default factory botloader binary for the Cheetah v1.1?
I've accidentaly overwrite bootloader on my board and now it won't start.
I would appriciate for any help, thanks!

Closed 2021-01-27.

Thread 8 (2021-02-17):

Compile for Cheetah

defconhaya, 2021-02-17:
Hi,
In the platformio.ini there are following lines:
```
[platformio]
src_dir      = Marlin
boards_dir   = buildroot/share/PlatformIO/boards
default_envs = mega2560
include_dir  = Marlin
```
but the board has an STM32F103 MCU
what changes have to be made in order to compile for FYSETC-Cheetah?

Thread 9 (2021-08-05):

v1.1 Schematic has heater pins swapped

sixtyfive, 2021-08-05:
According to https://raw.githubusercontent.com/FYSETC/FYSETC-Cheetah/master/hardware/1.1/Cheetah_Board%20V1.1%20SCH.pdf,

- bed heater: `PC7`
- tool heater: `PC6`

This is wrong. The actual pin assignment is:

- bed heater: `PC6`
- tool heater: `PC7`

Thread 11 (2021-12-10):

Smart filament detector on Cheetah 1.1b

kravviec, 2021-12-10:
How to find the pin for the filament detector on the cheetah 1.1b. I tried to configure BTT smart sensor with Klipper but can't find the pin number. Bad documentation- no luck.

mrskoku, 2021-12-11:
> How to find the pin for the filament detector on the cheetah 1.1b. I tried to configure BTT smart sensor with Klipper but can't find the pin number. Bad documentation- no luck.

https://github.com/MarlinFirmware/Marlin/blob/2.0.x/Marlin/src/pins/stm32f1/pins_FYSETC_CHEETAH.h

// Filament runout
//
#define FIL_RUNOUT_PIN                      PB5

kravviec, 2021-12-11:
Thanks, buddy, I'll try to run it. BTW maybe the manufacturer should consider supplementing the pinout table in the documentation?

mrskoku, 2021-12-11:
It should but support for this board is poor.

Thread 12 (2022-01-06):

What boot loader for Cheetah 1.1b?

ModMike, 2022-01-06:
I am using klipper and the documentation is conflicting.

! set says to use no boot loader option and the other is saying to use 20K boot loader. I have 3 of these boards and all of them have used klipper before. I can upload the firmware using stm32flash -w out/klipper.bin -v -i rts,-dtr,dtr /dev/ttyUSB0 but can never connect to Klipper.

All help very much appreciated.

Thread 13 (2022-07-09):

Cheetah 1.2b won't connect to Klipper

VinnyCordeiro, 2022-07-09:
I have followed all the instructions available on this repository on:
* how to update the bootloader;
* how to configure, compile, and install Klipper;
* and how to compile, and install the updated CH340 device driver on Linux.

All those previous steps were successful, but Klipper still fails to connect to the board. I've tried with Raspberry Pi OS Buster version and Bullseye version, neither work. I have even used the pins near the USB port to connect a FT232 breakout board I have to bypass the CH340 chip, but that also wasn't successful and Klipper still does not connect. I have no idea what's going on and need some help.

GerogeFu, 2022-08-02:
Try to use this OS image: https://www.dropbox.com/s/rwtf2i28a9i2v9n/SAMFi-RaspberryPi_v0.1.zip?dl=0

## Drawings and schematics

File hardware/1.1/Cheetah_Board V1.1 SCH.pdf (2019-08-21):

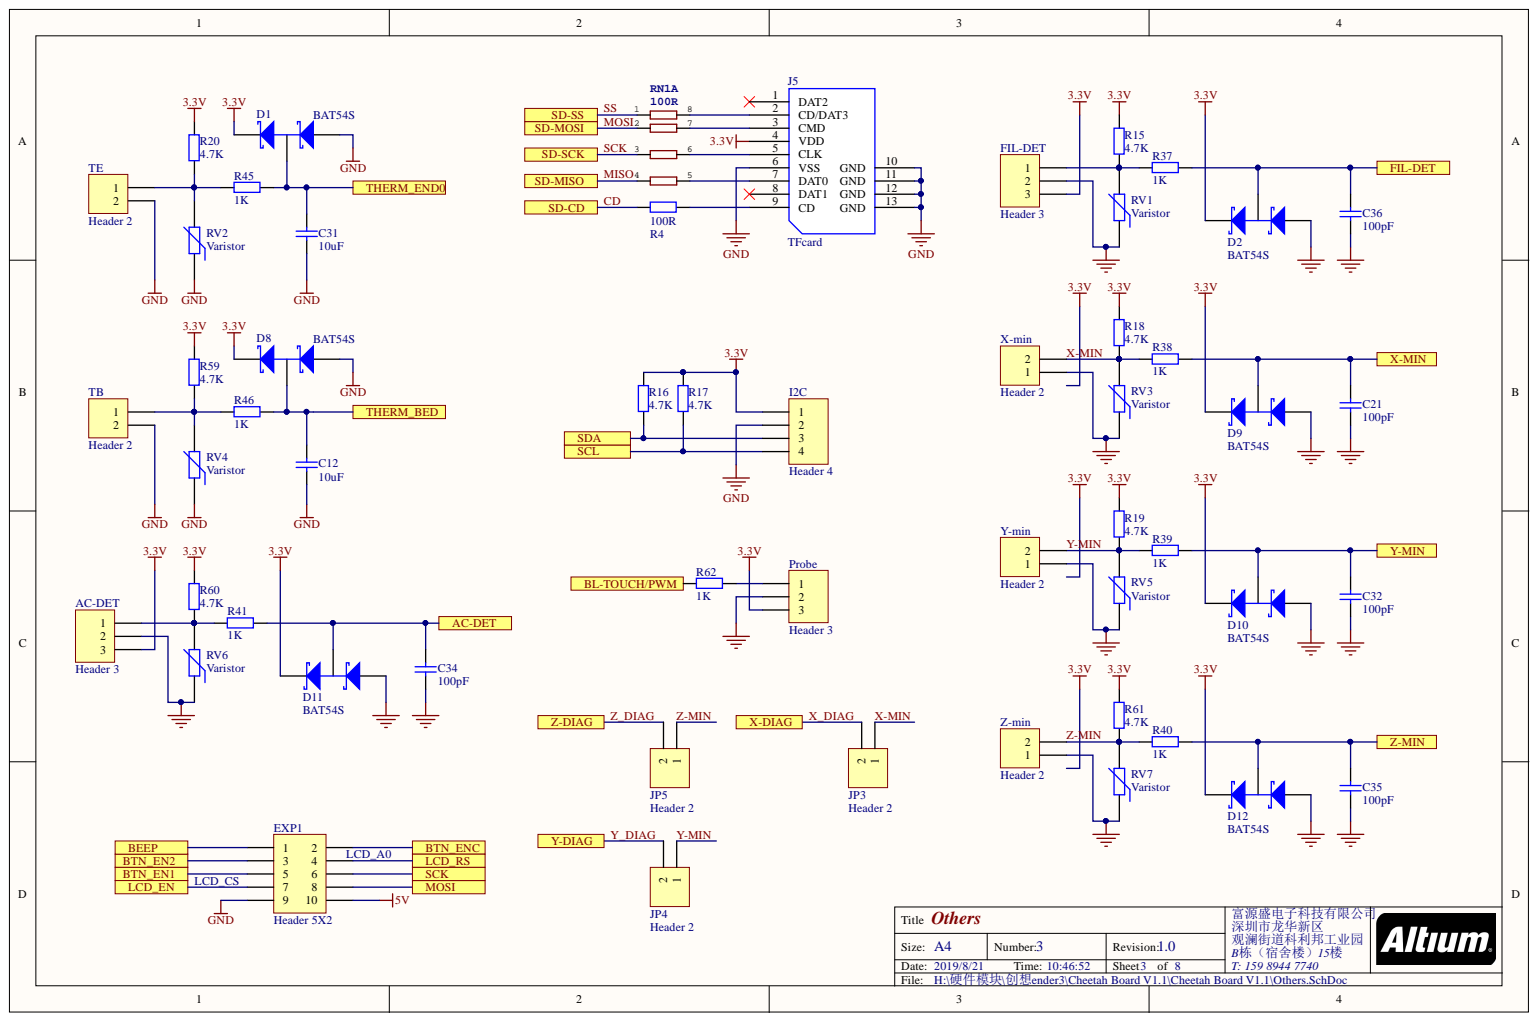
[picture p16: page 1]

Others Title | 富源盛电子科技有限公司 深圳市龙华新区 观澜街道科利邦工业园 T: 159 8944 7740

Size: A4 | Number: 3 | Revision: 1.0 | B栋（宿舍楼）15楼 8
Date: 2019/8/21 Time: 10:46:52 | | Sheet of

H:\硬件模块\创想ender3\Cheetah Board V1.1\Cheetah Board V1.1\Others.SchDoc
File:

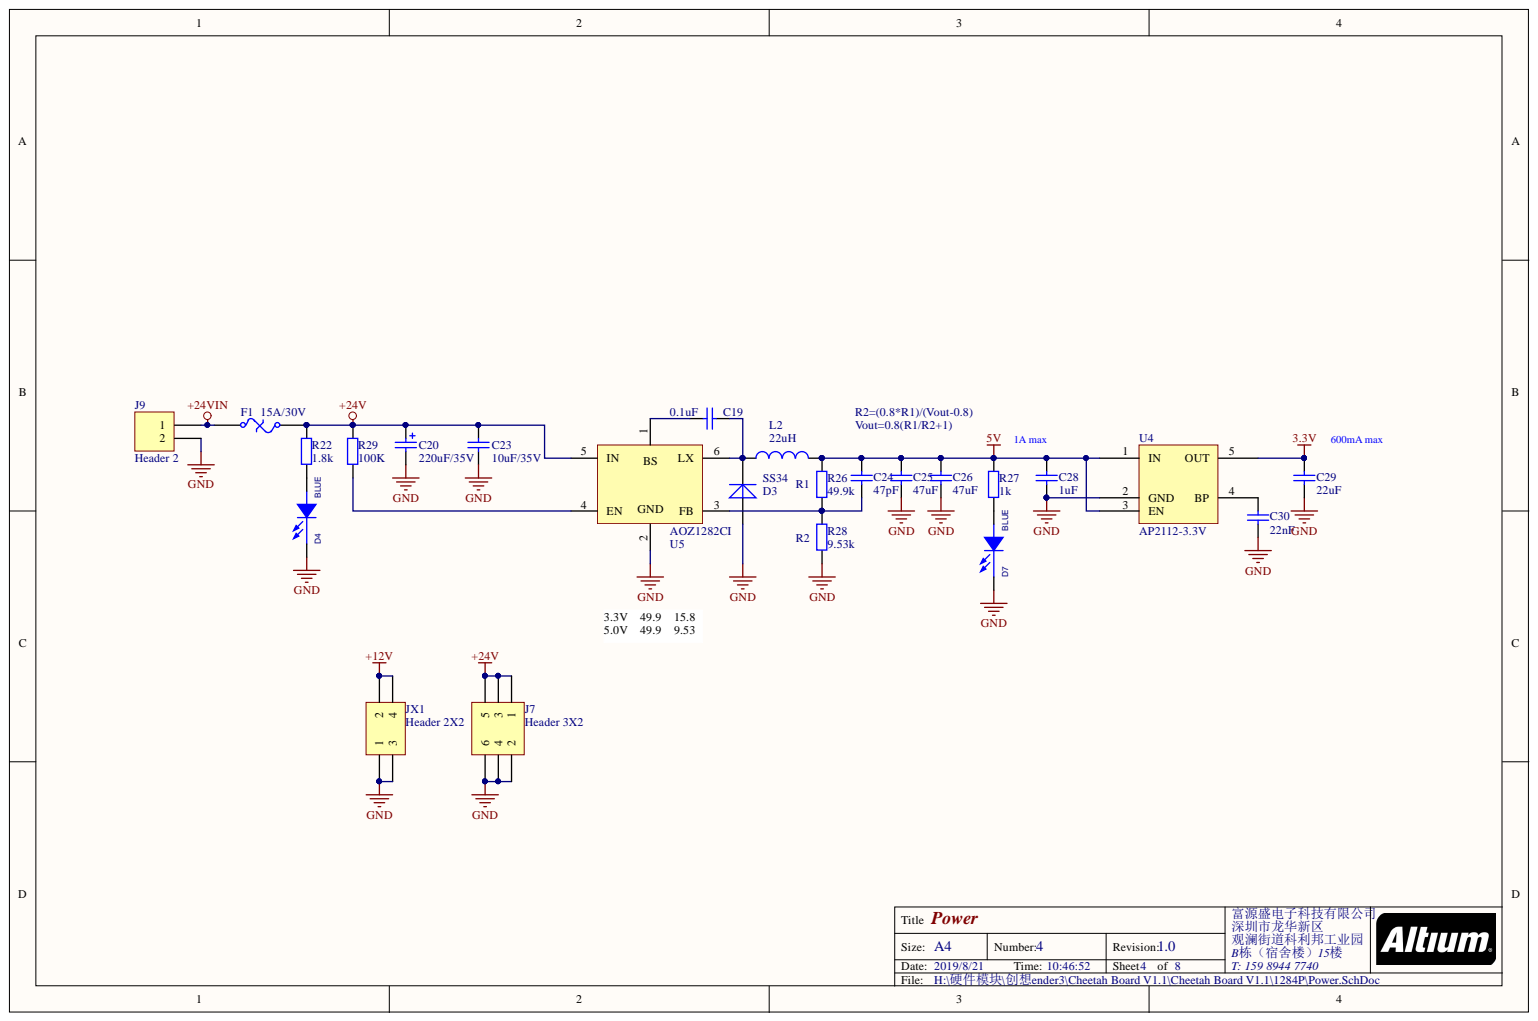
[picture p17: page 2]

Power Title | 富源盛电子科技有限公司 深圳市龙华新区 观澜街道科利邦工业园 T: 159 8944 7740

Size: A4 | Number: 4 | Revision: 1.0 | B栋（宿舍楼）15楼 8

H:\硬件模块\创想ender3\Cheetah Board V1.1\Cheetah Board V1.1\1284P\Power.SchDoc

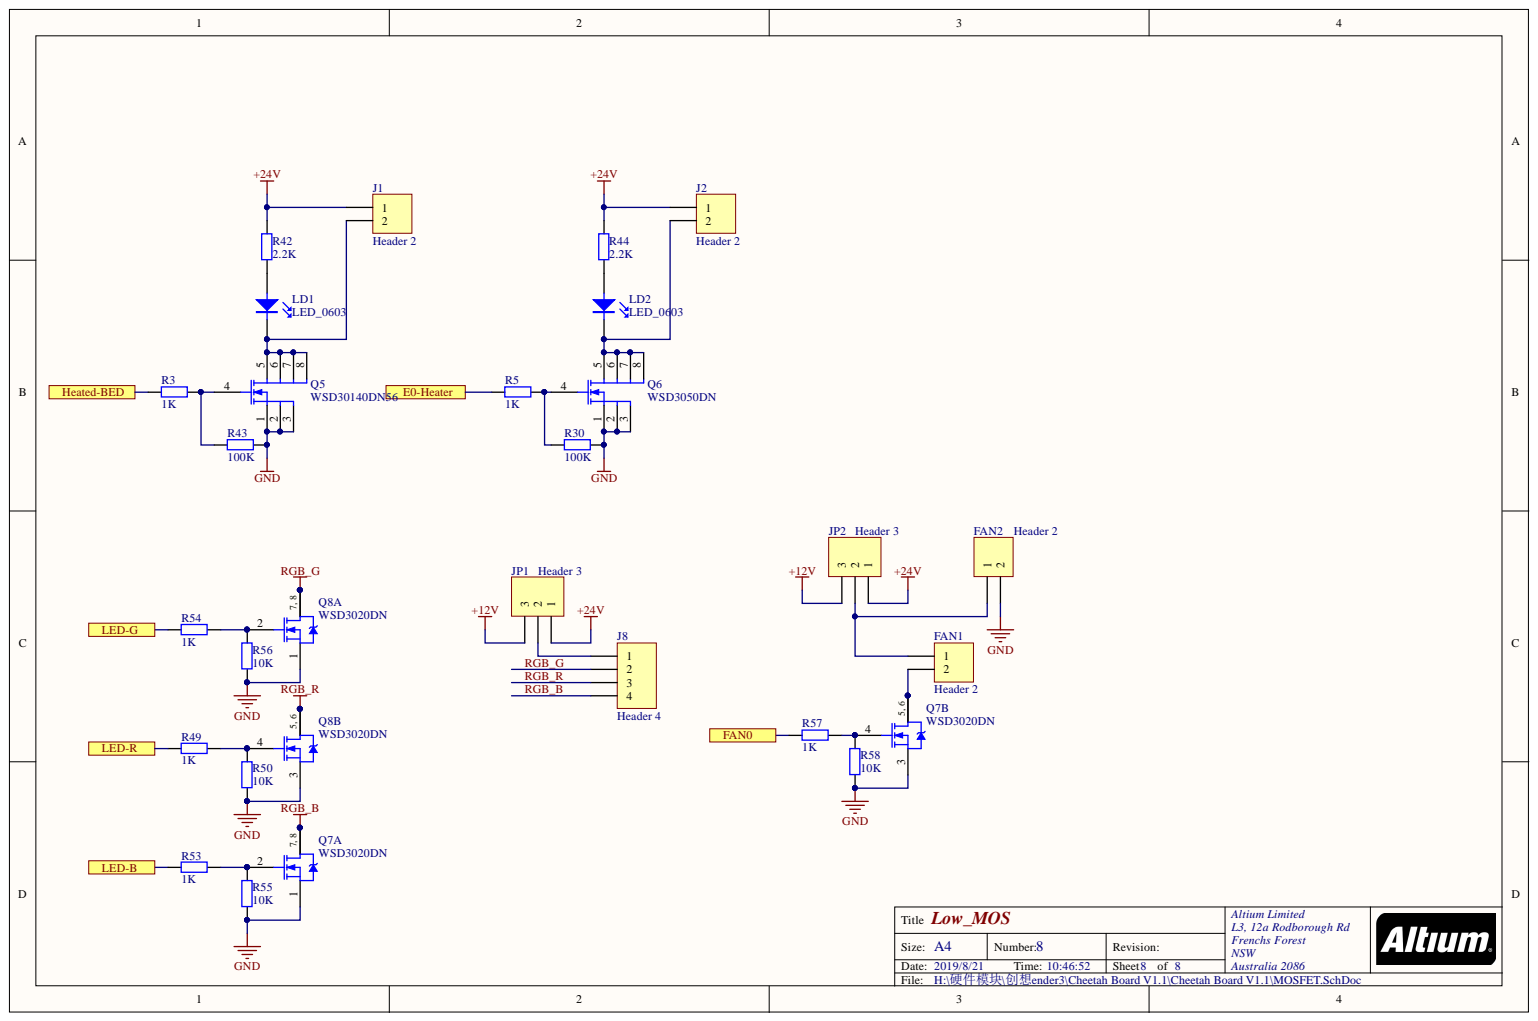
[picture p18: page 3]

Low_MOS Title | Altium Limited L3, 12a Rodborough Rd Frenchs Forest NSW Australia 2086

Size: A4 | Number: 8 | Revision:

H:\硬件模块\创想ender3\Cheetah Board V1.1\Cheetah Board V1.1\MOSFET.SchDoc

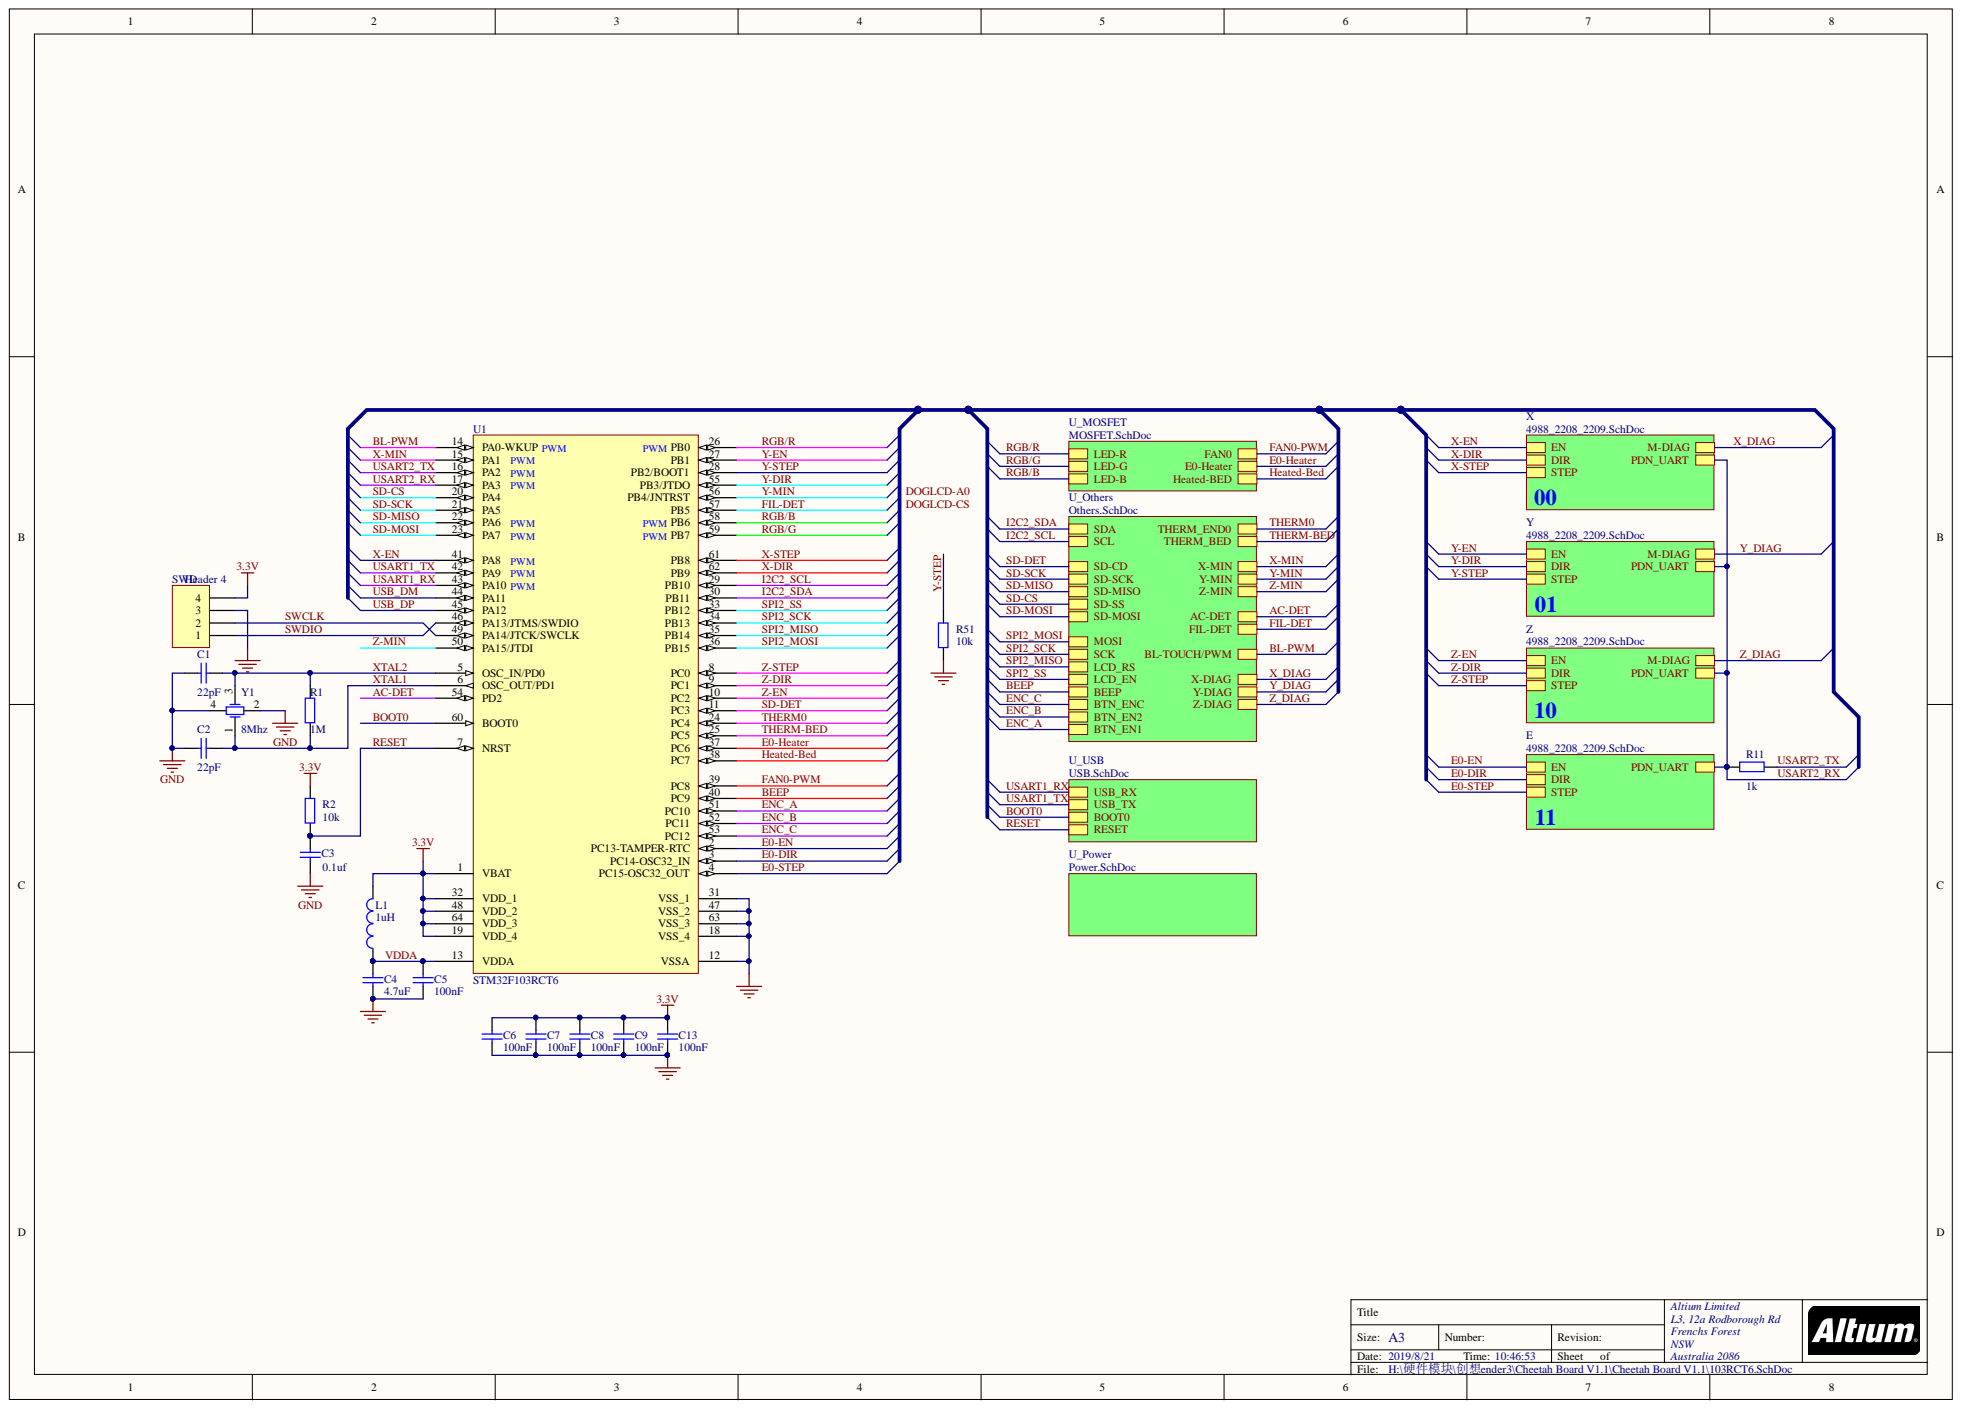
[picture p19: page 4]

Ti t l e | A l t ium Li m i ted L3, 12a Rodborough R d F renchs Fores t NSW Aus t ral ia 2086

Size: A | Number : | Revi s ion:

Ti me: | | Sheet of

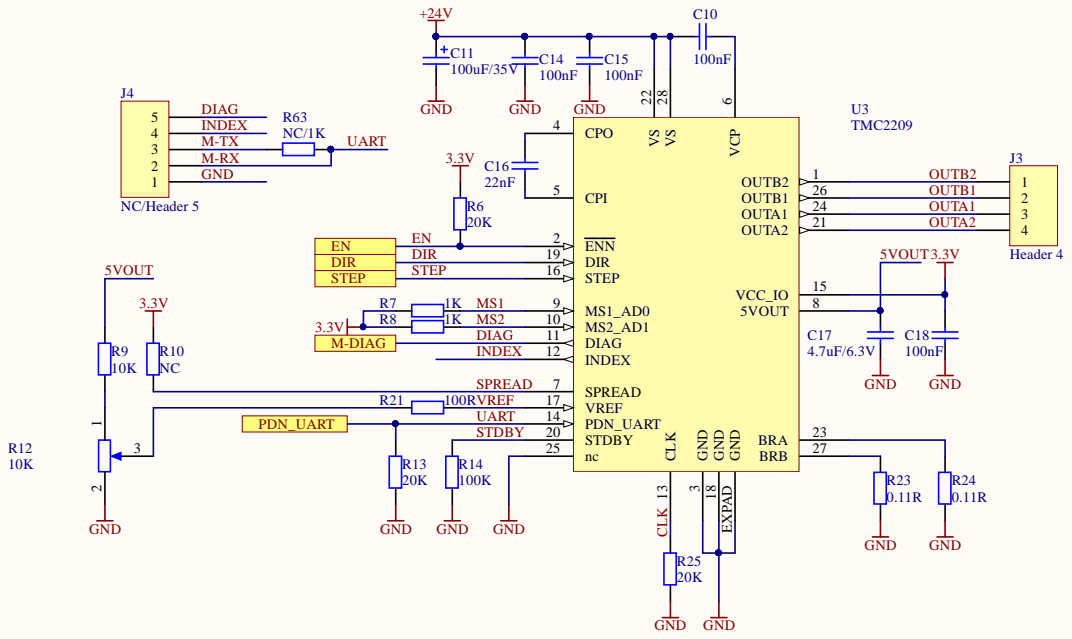
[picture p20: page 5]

VREF 17

STDBY | STDBY 20

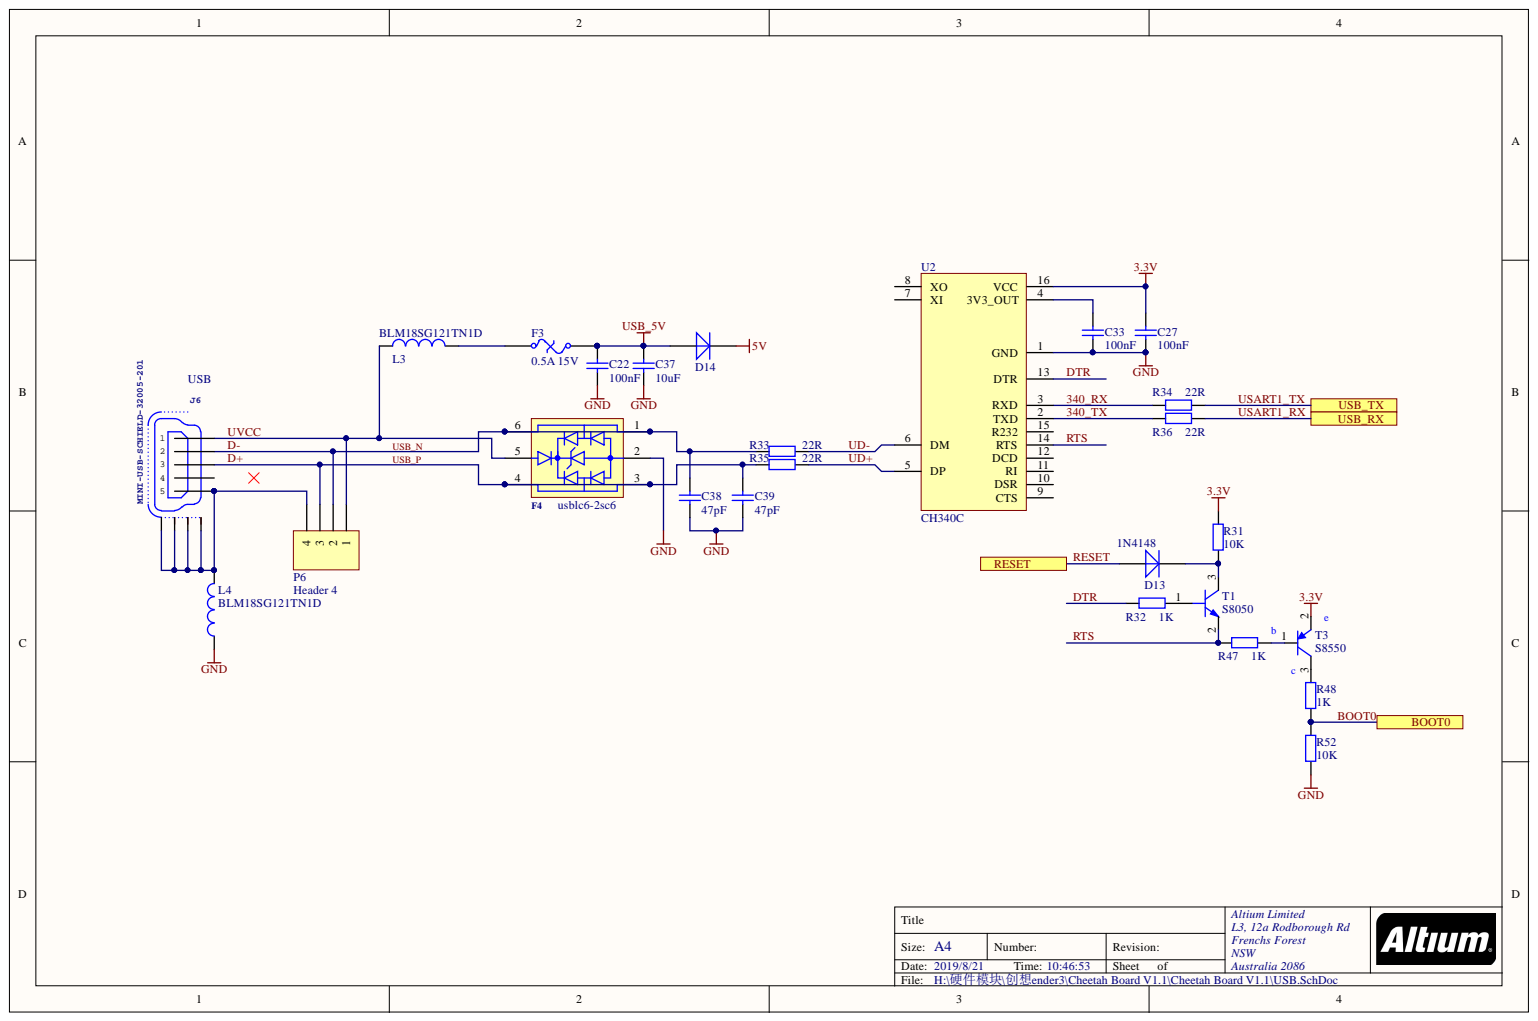
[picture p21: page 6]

D-
D+

USB_N | 5

Title | Altium Limited L3, 12a Rodborough Rd Frenchs Forest NSW Australia 2086

Size: A4 | Number: | Revision:
2019/8/21 10:46:53

H:\硬件模块\创想ender3\Cheetah Board V1.1\Cheetah Board V1.1\USB.SchDoc

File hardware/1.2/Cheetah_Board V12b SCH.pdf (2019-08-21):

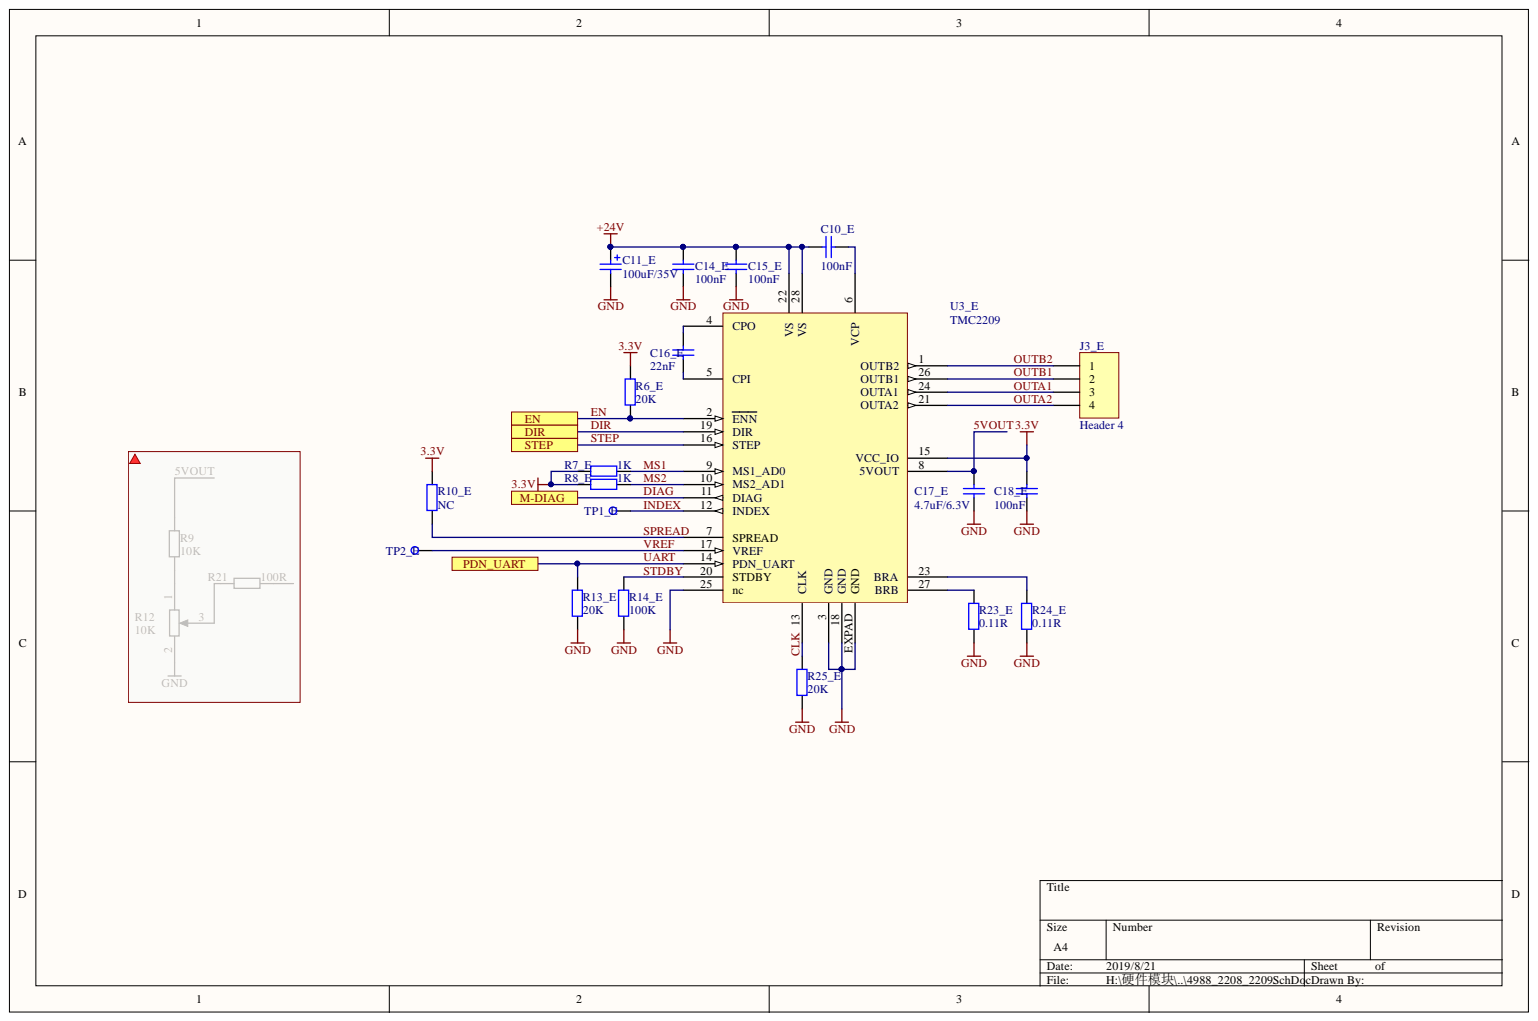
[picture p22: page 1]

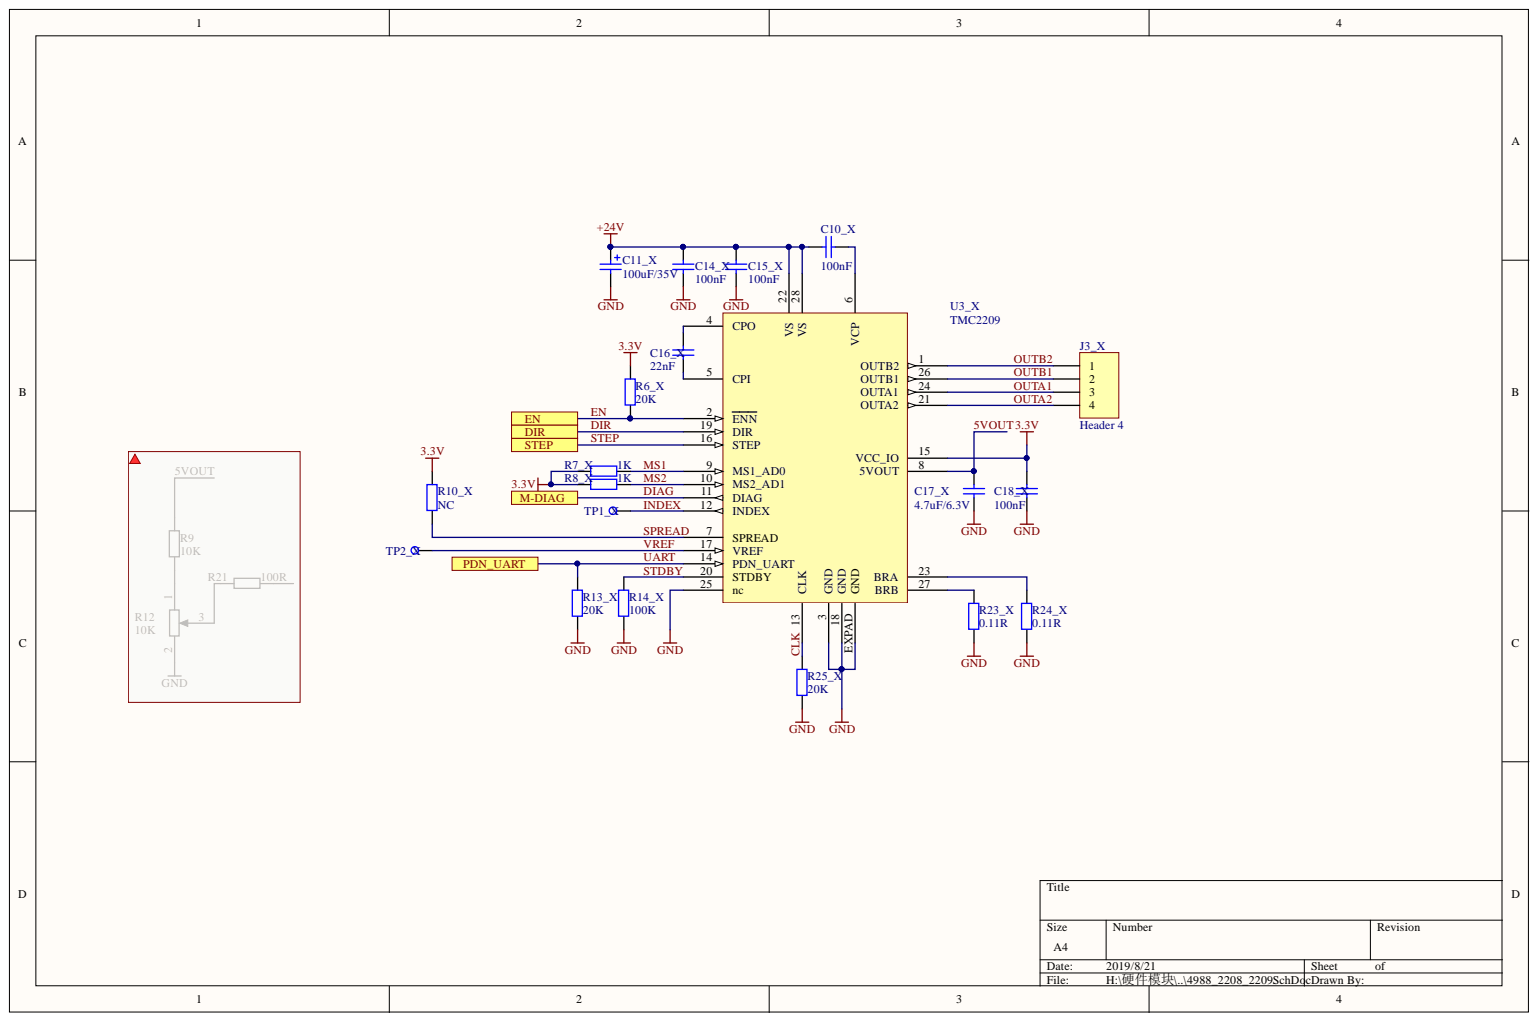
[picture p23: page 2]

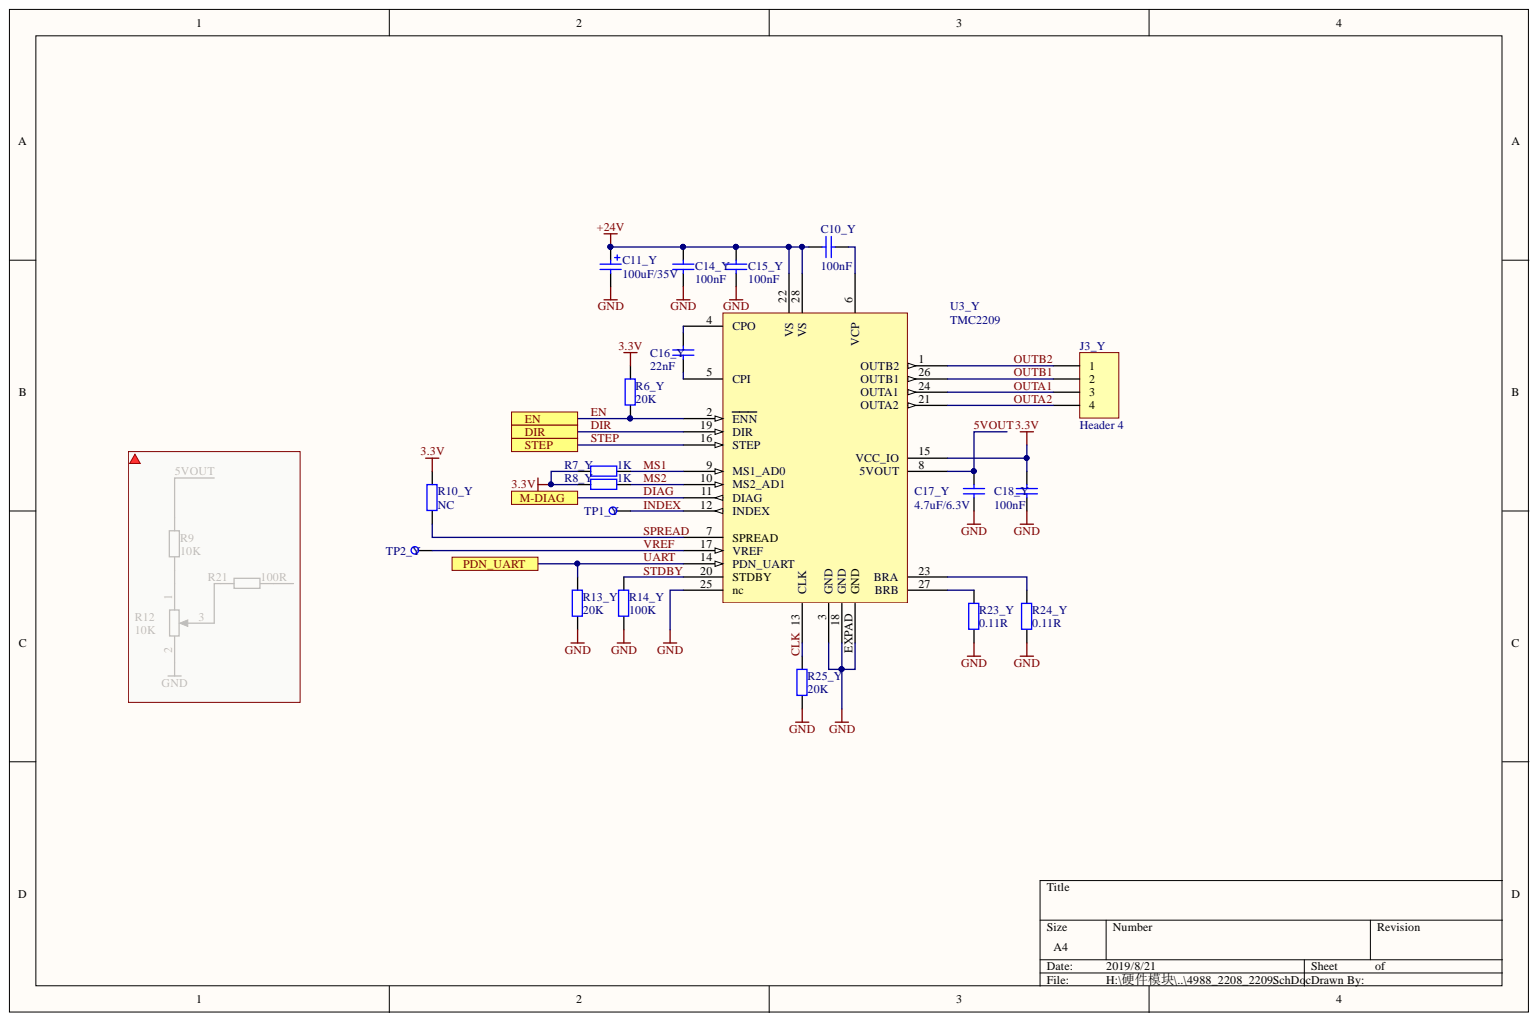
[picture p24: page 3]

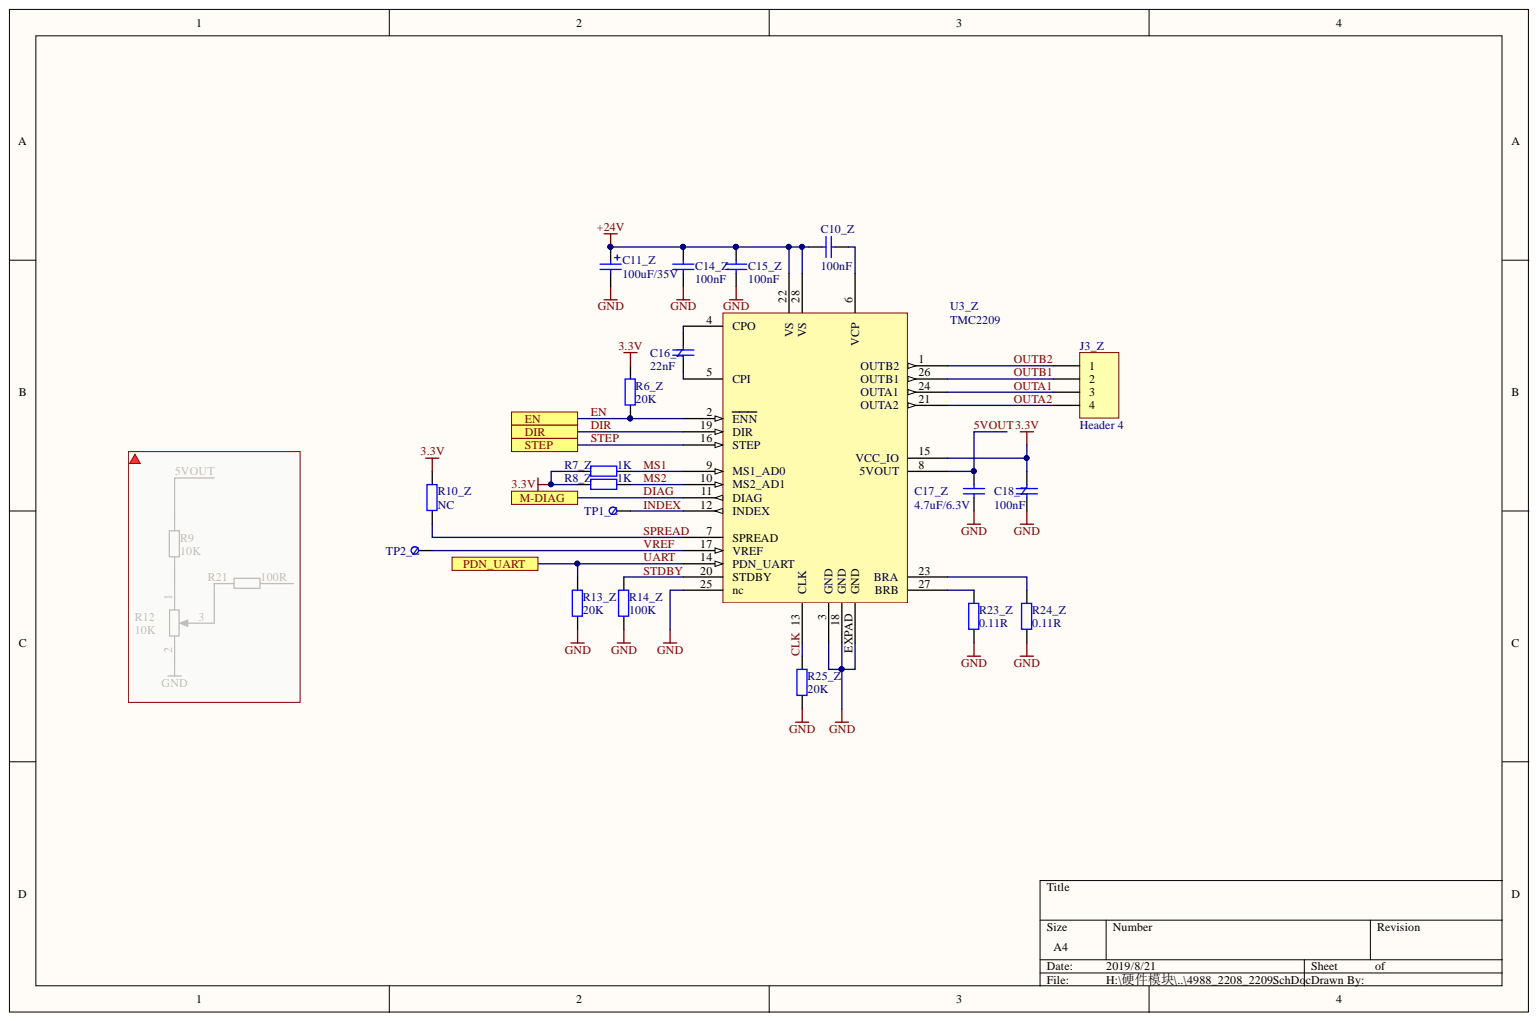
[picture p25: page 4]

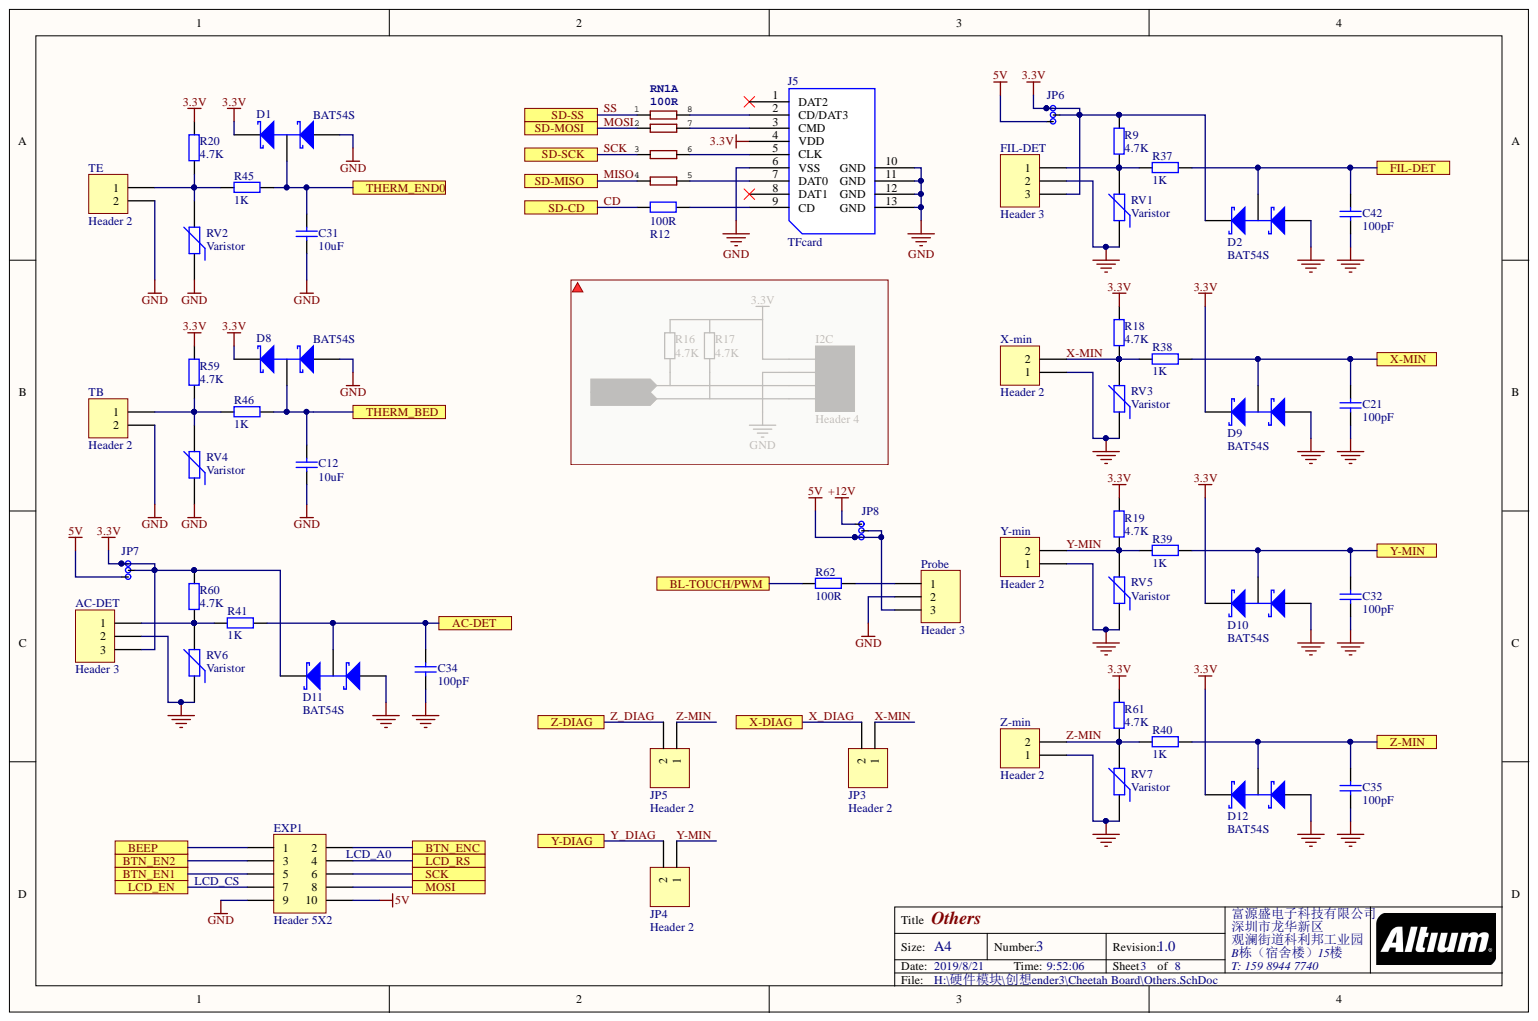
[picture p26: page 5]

Others Title | 富源盛电子科技有限公司 深圳市龙华新区 观澜街道科利邦工业园 T: 159 8944 7740

Size: A4 | Number: 3 | Revision: 1.0 | B栋（宿舍楼）15楼 8
Date: 2019/8/21 Time: 9:52:06 | | Sheet of

H:\硬件模块\创想ender3\Cheetah Board\Others.SchDoc
File:

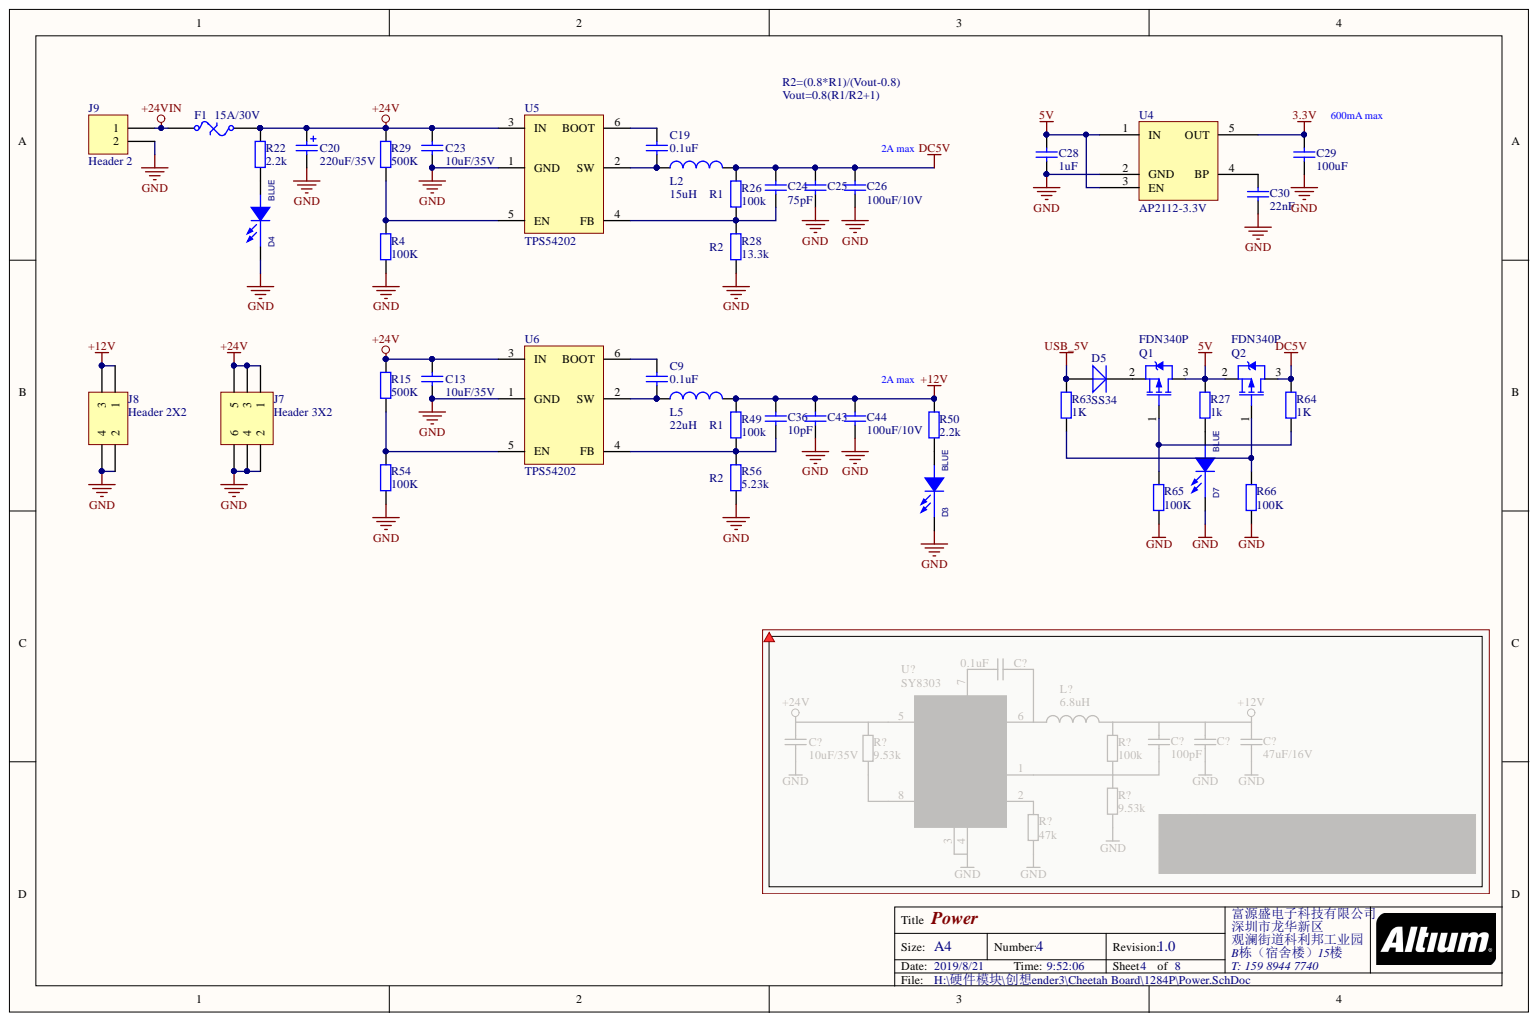
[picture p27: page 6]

Power T i t l e | 富源盛电子科技有限公司 深圳市龙华新区 观澜街道科利邦工业园 B栋（宿舍楼）15楼 T: 1 9 8 4 7

Size: A4 | N umber: 4 | Rev i s i o n : 1.0

/ / T ime: : : | | Sheet o f


GND 3

BED

Low_MOS Title | Altium Limited L3, 12a Rodborough Rd Frenchs Forest NSW Australia 2086

Size: A4 | Number: 8 | Revision:
2019/8/21 Time: 9:52:06 | | Sheet of 8

H:\硬件模块\创想ender3\Cheetah Board\MOSFET.SchDoc
File:


PWM
Bed FAN0-PWM X-STEP X-DIR Y-EN Y-STEP Y-DIR Z-EN E0-EN E0-STEP E0-DIR

Ti t l e | A l t ium Li m i ted L3, 12a Rodborough R d F renchs Fores t NSW Aus t ral ia 2086

Size: A | Number : | Revi s ion:
2019/8/21 Ti me: 9:52:06 | | Sheet of


U VCC | US B_N
D -

T i t l e | A l t i u m Li m i ted L3, 1 2 a R o d b o ro u g h R d F rench s F o res t NS W A u s t r a l i a 2

Size: A4 | N umber: | Rev i s i o n :

/ / T ime: : : | | Sheet o f




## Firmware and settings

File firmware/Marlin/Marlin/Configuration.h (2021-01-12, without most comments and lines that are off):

#pragma once
#define CONFIGURATION_H_VERSION 020007
#define STRING_CONFIG_H_AUTHOR "(thisiskeithb, Ender-3)" // Who made the changes.
#define SHOW_BOOTSCREEN
#define SHOW_CUSTOM_BOOTSCREEN
#define CUSTOM_STATUS_SCREEN_IMAGE
#define SERIAL_PORT 1
#define BAUDRATE 115200
  #define MOTHERBOARD BOARD_FYSETC_CHEETAH_V12
#define CUSTOM_MACHINE_NAME "Ender-3"
#define EXTRUDERS 1
#define DEFAULT_NOMINAL_FILAMENT_DIA 1.75
#define TEMP_SENSOR_0 1
#define TEMP_SENSOR_1 0
#define TEMP_SENSOR_2 0
#define TEMP_SENSOR_3 0
#define TEMP_SENSOR_4 0
#define TEMP_SENSOR_5 0
#define TEMP_SENSOR_6 0
#define TEMP_SENSOR_7 0
#define TEMP_SENSOR_BED 1
#define TEMP_SENSOR_PROBE 0
#define TEMP_SENSOR_CHAMBER 0
#define DUMMY_THERMISTOR_998_VALUE 25
#define DUMMY_THERMISTOR_999_VALUE 100
#define MAX_REDUNDANT_TEMP_SENSOR_DIFF 10
#define TEMP_RESIDENCY_TIME     10  // (seconds) Time to wait for hotend to "settle" in M109
#define TEMP_WINDOW              1  // (°C) Temperature proximity for the "temperature reached" timer
#define TEMP_HYSTERESIS          3  // (°C) Temperature proximity considered "close enough" to the target
#define TEMP_BED_RESIDENCY_TIME 10  // (seconds) Time to wait for bed to "settle" in M190
#define TEMP_BED_WINDOW          1  // (°C) Temperature proximity for the "temperature reached" timer
#define TEMP_BED_HYSTERESIS      3  // (°C) Temperature proximity considered "close enough" to the target
#define HEATER_0_MINTEMP   5
#define HEATER_1_MINTEMP   5
#define HEATER_2_MINTEMP   5
#define HEATER_3_MINTEMP   5
#define HEATER_4_MINTEMP   5
#define HEATER_5_MINTEMP   5
#define HEATER_6_MINTEMP   5
#define HEATER_7_MINTEMP   5
#define BED_MINTEMP        5
#define HEATER_0_MAXTEMP 275
#define HEATER_1_MAXTEMP 275
#define HEATER_2_MAXTEMP 275
#define HEATER_3_MAXTEMP 275
#define HEATER_4_MAXTEMP 275
#define HEATER_5_MAXTEMP 275
#define HEATER_6_MAXTEMP 275
#define HEATER_7_MAXTEMP 275
#define BED_MAXTEMP      125
#define PIDTEMP
#define BANG_MAX 255     // Limits current to nozzle while in bang-bang mode; 255=full current
#define PID_MAX BANG_MAX // Limits current to nozzle while PID is active (see PID_FUNCTIONAL_RANGE below); 255=full current
#define PID_K1 0.95      // Smoothing factor within any PID loop
  #define PID_EDIT_MENU         // Add PID editing to the "Advanced Settings" menu. (~700 bytes of PROGMEM)
  #define PID_AUTOTUNE_MENU     // Add PID auto-tuning to the "Advanced Settings" menu. (~250 bytes of PROGMEM)
    #define DEFAULT_Kp  21.73
    #define DEFAULT_Ki   1.54
    #define DEFAULT_Kd  76.55
#define MAX_BED_POWER 255 // limits duty cycle to bed; 255=full current
  #define PID_FUNCTIONAL_RANGE 10 // If the temperature difference between the target temperature and the actual temperature
#define PREVENT_COLD_EXTRUSION
#define EXTRUDE_MINTEMP 170
#define PREVENT_LENGTHY_EXTRUDE
#define EXTRUDE_MAXLENGTH 200
#define THERMAL_PROTECTION_HOTENDS // Enable thermal protection for all extruders
#define THERMAL_PROTECTION_BED     // Enable thermal protection for the heated bed
#define THERMAL_PROTECTION_CHAMBER // Enable thermal protection for the heated chamber
#define USE_XMIN_PLUG
#define USE_YMIN_PLUG
#define USE_ZMIN_PLUG
#define USE_XMAX_PLUG
#define USE_YMAX_PLUG
#define USE_ZMAX_PLUG
#define ENDSTOPPULLUPS
#define X_MIN_ENDSTOP_INVERTING false // Set to true to invert the logic of the endstop.
#define Y_MIN_ENDSTOP_INVERTING false // Set to true to invert the logic of the endstop.
#define Z_MIN_ENDSTOP_INVERTING false // Set to true to invert the logic of the endstop.
#define X_MAX_ENDSTOP_INVERTING false // Set to true to invert the logic of the endstop.
#define Y_MAX_ENDSTOP_INVERTING false // Set to true to invert the logic of the endstop.
#define Z_MAX_ENDSTOP_INVERTING false // Set to true to invert the logic of the endstop.
#define Z_MIN_PROBE_ENDSTOP_INVERTING false // Set to true to invert the logic of the probe.
#define X_DRIVER_TYPE  TMC2208
#define Y_DRIVER_TYPE  TMC2208
#define Z_DRIVER_TYPE  TMC2208
#define E0_DRIVER_TYPE TMC2208
#define DEFAULT_AXIS_STEPS_PER_UNIT   { 80, 80, 400, 93 }
#define DEFAULT_MAX_FEEDRATE          { 300, 300, 5, 25 }
#define DEFAULT_MAX_ACCELERATION      { 500, 500, 100, 5000 }
#define DEFAULT_ACCELERATION          500    // X, Y, Z and E acceleration for printing moves
#define DEFAULT_RETRACT_ACCELERATION  500    // E acceleration for retracts
#define DEFAULT_TRAVEL_ACCELERATION   500    // X, Y, Z acceleration for travel (non printing) moves
#define DEFAULT_EJERK    5.0  // May be used by Linear Advance
  #define JUNCTION_DEVIATION_MM 0.08  // (mm) Distance from real junction edge
  #define JD_HANDLE_SMALL_SEGMENTS    // Use curvature estimation instead of just the junction angle
#define Z_MIN_PROBE_USES_Z_MIN_ENDSTOP_PIN
#define NOZZLE_TO_PROBE_OFFSET { 10, 10, 0 }
#define PROBING_MARGIN 10
#define XY_PROBE_SPEED (133*60)
#define Z_PROBE_SPEED_FAST HOMING_FEEDRATE_Z
#define Z_PROBE_SPEED_SLOW (Z_PROBE_SPEED_FAST / 2)
#define Z_CLEARANCE_DEPLOY_PROBE   10 // Z Clearance for Deploy/Stow
#define Z_CLEARANCE_BETWEEN_PROBES  5 // Z Clearance between probe points
#define Z_CLEARANCE_MULTI_PROBE     5 // Z Clearance between multiple probes
#define Z_PROBE_LOW_POINT          -2 // Farthest distance below the trigger-point to go before stopping
#define Z_PROBE_OFFSET_RANGE_MIN -20
#define Z_PROBE_OFFSET_RANGE_MAX 20
#define X_ENABLE_ON 0
#define Y_ENABLE_ON 0
#define Z_ENABLE_ON 0
#define E_ENABLE_ON 0 // For all extruders
#define DISABLE_X false
#define DISABLE_Y false
#define DISABLE_Z false
#define DISABLE_E false             // Disable the extruder when not stepping
#define INVERT_X_DIR true
#define INVERT_Y_DIR true
#define INVERT_Z_DIR true
#define INVERT_E0_DIR true
#define INVERT_E1_DIR false
#define INVERT_E2_DIR false
#define INVERT_E3_DIR false
#define INVERT_E4_DIR false
#define INVERT_E5_DIR false
#define INVERT_E6_DIR false
#define INVERT_E7_DIR false
#define X_HOME_DIR 1
#define Y_HOME_DIR 1
#define Z_HOME_DIR -1
#define X_BED_SIZE 235
#define Y_BED_SIZE 235
#define X_MIN_POS 0
#define Y_MIN_POS 0
#define Z_MIN_POS 0
#define X_MAX_POS X_BED_SIZE
#define Y_MAX_POS Y_BED_SIZE
#define Z_MAX_POS 250
#define MIN_SOFTWARE_ENDSTOPS
  #define MIN_SOFTWARE_ENDSTOP_X
  #define MIN_SOFTWARE_ENDSTOP_Y
  #define MIN_SOFTWARE_ENDSTOP_Z
#define MAX_SOFTWARE_ENDSTOPS
  #define MAX_SOFTWARE_ENDSTOP_X
  #define MAX_SOFTWARE_ENDSTOP_Y
  #define MAX_SOFTWARE_ENDSTOP_Z
#define Z_SAFE_HOMING
  #define Z_SAFE_HOMING_X_POINT X_CENTER  // X point for Z homing
  #define Z_SAFE_HOMING_Y_POINT Y_CENTER  // Y point for Z homing
#define HOMING_FEEDRATE_XY (20*60)
#define HOMING_FEEDRATE_Z  (4*60)
#define VALIDATE_HOMING_ENDSTOPS
#define EEPROM_SETTINGS     // Persistent storage with M500 and M501
#define EEPROM_CHITCHAT       // Give feedback on EEPROM commands. Disable to save PROGMEM.
#define EEPROM_BOOT_SILENT    // Keep M503 quiet and only give errors during first load
#define HOST_KEEPALIVE_FEATURE        // Disable this if your host doesn't like keepalive messages
#define DEFAULT_KEEPALIVE_INTERVAL 2  // Number of seconds between "busy" messages. Set with M113.
#define BUSY_WHILE_HEATING            // Some hosts require "busy" messages even during heating
#define PREHEAT_1_LABEL       "PLA"
#define PREHEAT_1_TEMP_HOTEND 185
#define PREHEAT_1_TEMP_BED     45
#define PREHEAT_1_FAN_SPEED   255 // Value from 0 to 255
#define PREHEAT_2_LABEL       "ABS"
#define PREHEAT_2_TEMP_HOTEND 240
#define PREHEAT_2_TEMP_BED     70
#define PREHEAT_2_FAN_SPEED   255 // Value from 0 to 255
#define PRINTJOB_TIMER_AUTOSTART
#define LCD_LANGUAGE en
#define DISPLAY_CHARSET_HD44780 JAPANESE
#define LCD_INFO_SCREEN_STYLE 0
#define SDSUPPORT
#define SPEAKER
#define FYSETC_GENERIC_12864_1_1 // Larger display with basic ON/OFF backlight.
#define SOFT_PWM_SCALE 0
#define SERVO_DELAY { 300 }

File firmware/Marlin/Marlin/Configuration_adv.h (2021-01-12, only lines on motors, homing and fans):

#define E0_AUTO_FAN_PIN -1
#define E1_AUTO_FAN_PIN -1
#define E2_AUTO_FAN_PIN -1
#define E3_AUTO_FAN_PIN -1
#define E4_AUTO_FAN_PIN -1
#define E5_AUTO_FAN_PIN -1
#define E6_AUTO_FAN_PIN -1
#define E7_AUTO_FAN_PIN -1
#define CHAMBER_AUTO_FAN_PIN -1
#define HOMING_BUMP_MM      { 5, 5, 2 }       // (mm) Backoff from endstops after first bump
#define HOMING_BUMP_DIVISOR { 2, 2, 4 }       // Re-Bump Speed Divisor (Divides the Homing Feedrate)
#define QUICK_HOME                          // If G28 contains XY do a diagonal move first
#define MICROSTEP_MODES { 16, 16, 16, 16, 16, 16 } // [1,2,4,8,16]
    #define X_CURRENT       580        // (mA) RMS current. Multiply by 1.414 for peak current.
    #define X_CURRENT_HOME  X_CURRENT  // (mA) RMS current for sensorless homing
    #define X_MICROSTEPS     16    // 0..256
    #define Y_CURRENT       580
    #define Y_CURRENT_HOME  Y_CURRENT
    #define Y_MICROSTEPS     16
    #define Z_CURRENT       580
    #define Z_CURRENT_HOME  Z_CURRENT
    #define Z_MICROSTEPS     16
    #define E0_CURRENT      650
    #define E0_MICROSTEPS    16
  #define X_HYBRID_THRESHOLD     100  // [mm/s]
  #define X2_HYBRID_THRESHOLD    100
  #define Y_HYBRID_THRESHOLD     100
  #define Y2_HYBRID_THRESHOLD    100
  #define Z_HYBRID_THRESHOLD       3
  #define Z2_HYBRID_THRESHOLD      3
  #define Z3_HYBRID_THRESHOLD      3
  #define Z4_HYBRID_THRESHOLD      3
  #define E0_HYBRID_THRESHOLD     30
  #define E1_HYBRID_THRESHOLD     30
  #define E2_HYBRID_THRESHOLD     30
  #define E3_HYBRID_THRESHOLD     30
  #define E4_HYBRID_THRESHOLD     30
  #define E5_HYBRID_THRESHOLD     30
  #define E6_HYBRID_THRESHOLD     30
  #define E7_HYBRID_THRESHOLD     30

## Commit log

2021-01-11 Update doc stuctures
    [Cheetah_MainBoard_V11.DWG]
2021-01-11 Upload raw firmware
    [Configuration.h, Configuration_adv.h]
2021-01-12 upload ender-5 firmwares
    [Configuration.h, Configuration_adv.h]
2021-03-02 Upload Cheetah v1.2 Klipper pre-build firmware
2021-07-07 Update klipper related stuff
2021-07-15 Update input vol para
2021-09-23 Add pin definition
2022-07-15 Update README and config
    [printer.cfg, stm32_mini12864.cfg]

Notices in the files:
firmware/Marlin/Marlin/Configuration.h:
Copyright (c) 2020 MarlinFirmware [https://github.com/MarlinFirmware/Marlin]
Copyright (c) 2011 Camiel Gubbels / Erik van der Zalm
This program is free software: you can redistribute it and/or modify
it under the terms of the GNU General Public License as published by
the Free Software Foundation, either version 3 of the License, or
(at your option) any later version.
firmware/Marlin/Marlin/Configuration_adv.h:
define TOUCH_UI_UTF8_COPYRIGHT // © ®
